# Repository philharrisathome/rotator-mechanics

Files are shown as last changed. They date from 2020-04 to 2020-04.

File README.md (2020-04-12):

# rotator-mechanics

This is my branch of https://gitlab.com/librespacefoundation/satnogs/satnogs-rotator/-/tree/v3.1-pre-release, heavily modified for different drive motor strategy.

Full credit goes to the team at SatNOGS - if I can get this build working I'll look at merging it in.

---

# SatNOGS Rotator

Hardware for SatNOGS Rotator. This repository includes all needed source files for 3D printed (and other) parts of SatNOGS Rotator.

## Documentation

More information can be found in our [wiki](https://wiki.satnogs.org/SatNOGS_Rotator_v3).

## Repository policy - Naming Convention

According to F3 - [Form, Fit and function](https://en.wikipedia.org/wiki/Form,_fit_and_function) and
[Part number, wiki page](https://en.wikipedia.org/wiki/Part_number) some rules build about the naming
convention and versioning:
* C, custom parts, placed in rotator_parts file
* H, hardware parts, placed in shared file
* A, assemblies, placed in assemblies file
* All used part numbers are placed in part-number-list spreadsheet.
* Start the number from 1000, e.g. C1000-1.
* Dash -1 (odd), are parts from same family for example M5 screws with same DIN and different lengths.
* Dash -2 (even), are parts from same family but all features are mirrored.
* Small changes in the part (fit - aspect), not affect the part number but affected the variant (-n).
* Big changes in the part or assembly (form and function aspect), affect the part number, make a new one
and replace or remove the old one.
* When a part is ready, in the commit message only this part and the message contains the revision of the part and a
release note about the changes. If needed update the drawing inside the freecad.
Then commit all sub-assemblies and the main assembly which affected by the part or parts.
* In order to add a new part take a new part number according to the part number list (spreadsheet).
* When a part or assembly isn't ready for release, in commit message add WIP, work in progress, write the
changes must be done, refers to the issue.
* When all parts and assemblies are ready and working properly, a release is done with tagging the last commit
and a file with all fabrication files like *.stl, *.step, *.pdf (for drawings), *.dxf (for 2D parts) are generated
which each file is naming with pn_revN.*
* Master branch is most times under active development, so expect things to break.
* Assembly is broken down to specific groups, sub-assemlies. The first priority of assembly levels is to help the designer in
design process and not in the real assembly. The second priority is to make assemblies that helps in assembly process.
We never work on very large assemblies, due to limitation in CAD program.
* Try to use a coordinate system that is fit in the main assembly.
* Drawing revision does not exist, only part or assembly revision is modified. When a small change is done in drawing for example in text the revision isn't change because the part or assembly isn't change.

## Contribute

The main repository lives on [Gitlab](https://gitlab.com/librespacefoundation/satnogs/satnogs-rotator) and all Merge Request should happen there.

## License


Licensed under the [CERN OHLv1.2](LICENSE).

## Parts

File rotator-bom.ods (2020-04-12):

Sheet: DC Motor
Part | Qty To Buy | Qty In project | Sold in Packs of | Unit of Measure | Distributor | Ref | Distributor Ref | Project Section | Price | Cost to Project | Link
Aluminum Tube 6063 OD40 TH1.5 | 2 | 2 | 1 | PCE | Motedis | C1001-1 and C1001-3 | 2287 | Hardware | 0.9 | 1.8 | https://www.motedis.com/shop/Semi-finished-products/Circular-tube-anodized-DIN-6060/Circular-tube-40x15-anodized::1066.html
Shaft Side | 4 | 4 | 1 | PCE |  | C1010-3 |  | Custom Part |  | 0
Shaft Side Bearing Flange | 4 | 4 | 1 | PCE |  | C1011-3 |  | Custom Part |  | 0
Worm Wheel, 30T | 2 | 2 | 1 | PCE |  | C1020-1 |  | Custom Part |  | 0
Shaft Collar ID40 | 2 | 2 | 1 | PCE |  | C1021-1 |  | Custom Part |  | 0
Shaft Washer ID40 OD50 | 2 | 2 | 1 | PCE |  | C1022-1 |  | Custom Part |  | 0
Motor Mount | 2 | 2 | 1 | PCE |  | C1030-1 |  | Custom Part |  | 0
Encoder Gear | 2 | 2 | 1 | PCE |  | C1040-1 |  | Custom Part |  | 0
Homing Pin | 2 | 2 | 1 | PCE |  | C1041-1 |  | Custom Part |  | 0
End-Stop Mount | 2 | 2 | 1 | PCE |  | C1042-1 |  | Custom Part |  | 0
Encoder Mount | 2 | 2 | 1 | PCE |  | C1043-1 |  | Custom Part |  | 0
Aluminum Profil 20x20 B-type slot 6 L100 | 18 | 18 | 1 | PCE | Motedis | C1050-1 | 22206 | Custom Part | 0.3 | 5.4 | https://www.motedis.com/shop/Slot-profiles/Profile-20-B-Type-slot-6/Profile-20x20-B-type-slot-6::1.html
Aluminum Profil 20x20 B-type slot 6 L140 | 8 | 8 | 1 | PCE | Motedis | C1050-5 | 22206 | Custom Part | 0.45 | 3.6 | https://www.motedis.com/shop/Slot-profiles/Profile-20-B-Type-slot-6/Profile-20x20-B-type-slot-6::1.html
Threaded rod M5 DIN975 INOX A2, Worm Gear Shaft | 1 | 1 | 1 | m |  | C1060-1 |  | Hardware | 2.5 | 2.5
Worm Mount | 4 | 4 | 1 | PCE |  | C1061-3 and C1061-4 |  | Custom Part |  | 0
Worm Gear | 2 | 2 | 1 | PCE |  | C1062-1 |  | Custom Part | 10 | 20 | https://www.shapeways.com/
Deep groove ball bearing 625zz | 4 | 4 | 1 | PCE |  | H1011-1 |  | Hardware | 0.6 | 2.4
Deep groove ball bearing 6008zz | 4 | 4 | 1 | PCE |  | H1012-1 |  | Hardware | 4 | 16
Inner bracket B-type Tslot6 | 40 | 40 | 1 | PCE | Motedis | H1020-1 | 099I9006 | Hardware | 0.5 | 20 | https://www.motedis.com/shop/Slot-profile-accessories/Accessories-20-B-Typ-slot-6/Inner-bracket-20-steel-B-Type-slot-6::562.html
T-nut B-type slot 6 M4 | 32 | 32 | 1 | PCE | Motedis | H1021-1 | 096H06410 | Hardware | 0.2 | 6.4 | https://www.motedis.com/shop/Slot-profile-accessories/Accessories-20-B-Typ-slot-6/T-nut-B-type-slot-6-M4::555.html
M5 Nut DIN934 | 4 | 4 | 1 | PCE |  | H1030-1 |  | Hardware | 0.03 | 0.12
M5 Washer DIN125 | 6 | 6 | 1 | PCE |  | H1031-1 |  | Hardware | 0.03 | 0.18
Timing Pulley GT2 36T, bore 5mm, belt wide 6mm | 2 | 2 | 1 | PCE |  | H1040-1 |  | Hardware | 4.2 | 8.4
Timing Belt GT2, Wide 6mm, Length 158mm, Teeth 79 | 2 | 2 | 1 | PCE |  | H1200-1 |  | Hardware | 1.5 | 3
M3 Nut DIN934 | 26 | 26 | 1 | PCE |  | H1070-1 |  | Hardware | 0.03 | 0.78
M4 Nut DIN934 | 24 | 24 | 1 | PCE |  | H1080-1 |  | Hardware | 0.03 | 0.72
Set Screw M3 L10 DIN 914 | 16 | 16 | 1 | PCE |  | H1090-1 |  | Hardware | 0.2 | 3.2
Screw M4 L25 DIN912 | 16 | 16 | 1 | PCE |  | H1100-1 |  | Hardware | 0.05 | 0.8
Screw M4 L20 DIN912 | 8 | 8 | 1 | PCE |  | H1100-3 |  | Hardware | 0.07 | 0.56
Screw M4 L10 DIN912 | 30 | 30 | 1 | PCE |  | H1100-5 |  | Hardware | 0.08 | 2.4
Washer M4 DIN125 | 34 | 34 | 1 | PCE |  | H1110-1 |  | Hardware | 0.03 | 1.02
Screw M3 L10 DIN912 | 8 | 8 | 1 | PCE |  | H1120-1 |  | Hardware | 0.04 | 0.32
Screw M3 L12 DIN912 | 4 | 4 | 1 | PCE |  | H1120-3 |  | Hardware | 0.04 | 0.16
Washer M3 DIN125 | 12 | 12 | 1 | PCE |  | H1130-1 |  | Hardware | 0.03 | 0.36
U Bolts Clamp for 40mm Tube | 4 | 4 | 1 | PCE |  | H1060-1 |  | Hardware | 2 | 8
CAT5e UTP cable | 6 | 6 | 1 | m |  | H1170-5 |  | Electronics | 0.16 | 0.96
End stop switch SS0505 | 2 | 2 | 1 | PCE | HIGHLY | H1050-1 | SS0505A | Electronics | 0.7 | 1.4
Heat-shrinkable, OD 6.4mm for CAT5E cable | 1 | 1 | 1 | m |  | H1160-3 |  | Electronics | 0.3 | 0.3
Heat-shrinkable, OD 4.8mm, for end-stop cables | 1 | 1 | 1 | m |  | H1160-5 |  | Electronics | 0.25 | 0.25
Crimps for Dupont Female 2.54 pitch | 38 | 38 | 1 | PCE | pololu | H1180-1 | 1930 | Electronics | 0.06 | 2.28 | https://www.pololu.com/product/1930
Dupont, Housing Wire Female 4 Pins 2.54mm (2x2P) | 5 | 5 | 1 | PCE | pololu | H1190-1 | 1910 | Electronics | 0.06 | 0.3
Dupont, Housing Wire Female 3 Pins 2.54mm (1x3P) | 6 | 6 | 1 | PCE | pololu | H1190-3 | 1902 | Electronics | 0.04 | 0.24
ABS Filament for FDM 3D-printer | 1 | 1 | 1 | Kg |  | - |  | Hardware | 17 | 17
DC motor adapter | 2 | 2 | 1 | PCE |  | C1070-1 |  | Custom Part |  | 0
DC motor cover part #1 | 2 | 2 | 1 | PCE |  | C1071-1 |  | Custom Part |  | 0
DC motor cover part #2 | 2 | 2 | 1 | PCE |  | C1072-1 |  | Custom Part |  | 0
DC motor, D37mm L54mm, Gear ratio 50:1, 12V 200RPM 1.2Nm | 2 | 2 | 1 | PCE | pololu | H1001-1 | 1104 | Electronics | 25 | 50 | https://www.pololu.com/product/1104
Timing Pulley GT2 20T, bore 6mm, Belt width 6mm | 2 | 2 | 1 | PCE |  | H1041-3 |  | Hardware | 2.6 | 5.2
Screw M3L6 DIN965 | 8 | 8 | 1 | PCE |  | H1140-1 |  | Hardware | 0.04 | 0.32
Capacitor, MLCC - Leaded 0.1uF 50volts X7R 10% 5.0mm L/S | 2 | 2 | 1 | PCE | Mouser | H1150-1 | 75-1C20X7R104K050B | Electronics | 0.15 | 0.3 | https://gr.mouser.com/ProductDetail/Vishay-Sprague/1C20X7R104K050B/
Heat-shrinkable, OD 38.1mm | 1 | 1 | 1 | m |  | H1160-1 |  | Electronics | 1.8 | 1.8
Stranded Cable ~1.5mm^2 (16AWG) – Red | 1 | 1 | 1 | m |  | H1170-1 |  | Electronics | 0.5 | 0.5
Stranded Cable ~1.5mm^2 (16AWG) – Black | 1 | 1 | 1 | m |  | H1170-1 |  | Electronics | 0.5 | 0.5
 |  |  |  |  |  |  |  |  | Total | 188.97

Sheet: Stepper Motor
Part | Qty To Buy | Qty In project | Sold in Packs of | Unit of Measure | Distributor | Ref | Distributor Ref | Project Section | Price | Cost to Project | Link
Aluminum Tube 6063 OD40 TH1.5 | 2 | 2 | 1 | PCE | Motedis | C1001-1 and C1001-3 | 2287 | Hardware | 0.9 | 1.8 | https://www.motedis.com/shop/Semi-finished-products/Circular-tube-anodized-DIN-6060/Circular-tube-40x15-anodized::1066.html
Shaft Side | 4 | 4 | 1 | PCE |  | C1010-3 |  | Custom Part |  | 0
Shaft Side Bearing Flange | 4 | 4 | 1 | PCE |  | C1011-3 |  | Custom Part |  | 0
Worm Wheel, 30T | 2 | 2 | 1 | PCE |  | C1020-1 |  | Custom Part |  | 0
Shaft Collar ID40 | 2 | 2 | 1 | PCE |  | C1021-1 |  | Custom Part |  | 0
Shaft Washer ID40 OD50 | 2 | 2 | 1 | PCE |  | C1022-1 |  | Custom Part |  | 0
Motor Mount | 2 | 2 | 1 | PCE |  | C1030-1 |  | Custom Part |  | 0
Encoder Gear | 2 | 2 | 1 | PCE |  | C1040-1 |  | Custom Part |  | 0
Homing Pin | 2 | 2 | 1 | PCE |  | C1041-1 |  | Custom Part |  | 0
End-Stop Mount | 2 | 2 | 1 | PCE |  | C1042-1 |  | Custom Part |  | 0
Encoder Mount | 2 | 2 | 1 | PCE |  | C1043-1 |  | Custom Part |  | 0
Aluminum Profil 20x20 B-type slot 6 L100 | 18 | 18 | 1 | PCE | Motedis | C1050-1 | 22206 | Custom Part | 0.3 | 5.4 | https://www.motedis.com/shop/Slot-profiles/Profile-20-B-Type-slot-6/Profile-20x20-B-type-slot-6::1.html
Aluminum Profil 20x20 B-type slot 6 L140 | 8 | 8 | 1 | PCE | Motedis | C1050-5 | 22206 | Custom Part | 0.45 | 3.6 | https://www.motedis.com/shop/Slot-profiles/Profile-20-B-Type-slot-6/Profile-20x20-B-type-slot-6::1.html
Threaded rod M5 DIN975 INOX A2, Worm Gear Shaft | 1 | 1 | 1 | m |  | C1060-1 |  | Hardware | 2.5 | 2.5
Worm Mount | 4 | 4 | 1 | PCE |  | C1061-3 and C1061-4 |  | Custom Part |  | 0
Worm Gear | 2 | 2 | 1 | PCE |  | C1062-1 |  | Custom Part | 10 | 20 | https://www.shapeways.com/
Deep groove ball bearing 625zz | 4 | 4 | 1 | PCE |  | H1011-1 |  | Hardware | 0.6 | 2.4
Deep groove ball bearing 6008zz | 4 | 4 | 1 | PCE |  | H1012-1 |  | Hardware | 4 | 16
Inner bracket B-type Tslot6 | 40 | 40 | 1 | PCE | Motedis | H1020-1 | 099I9006 | Hardware | 0.5 | 20 | https://www.motedis.com/shop/Slot-profile-accessories/Accessories-20-B-Typ-slot-6/Inner-bracket-20-steel-B-Type-slot-6::562.html
T-nut B-type slot 6 M4 | 32 | 32 | 1 | PCE | Motedis | H1021-1 | 096H06410 | Hardware | 0.2 | 6.4 | https://www.motedis.com/shop/Slot-profile-accessories/Accessories-20-B-Typ-slot-6/T-nut-B-type-slot-6-M4::555.html
M5 Nut DIN934 | 4 | 4 | 1 | PCE |  | H1030-1 |  | Hardware | 0.03 | 0.12
M5 Washer DIN125 | 6 | 6 | 1 | PCE |  | H1031-1 |  | Hardware | 0.03 | 0.18
Timing Pulley GT2 36T, bore 5mm, belt wide 6mm | 2 | 2 | 1 | PCE |  | H1040-1 |  | Hardware | 4.2 | 8.4
Timing Belt GT2, Wide 6mm, Length 158mm, Teeth 79 | 2 | 2 | 1 | PCE |  | H1200-1 |  | Hardware | 1.5 | 3
M3 Nut DIN934 | 26 | 26 | 1 | PCE |  | H1070-1 |  | Hardware | 0.03 | 0.78
M4 Nut DIN934 | 24 | 24 | 1 | PCE |  | H1080-1 |  | Hardware | 0.03 | 0.72
Set Screw M3 L10 DIN 914 | 16 | 16 | 1 | PCE |  | H1090-1 |  | Hardware | 0.2 | 3.2
Screw M4 L25 DIN912 | 16 | 16 | 1 | PCE |  | H1100-1 |  | Hardware | 0.05 | 0.8
Screw M4 L20 DIN912 | 8 | 8 | 1 | PCE |  | H1100-3 |  | Hardware | 0.07 | 0.56
Screw M4 L10 DIN912 | 30 | 30 | 1 | PCE |  | H1100-5 |  | Hardware | 0.08 | 2.4
Washer M4 DIN125 | 34 | 34 | 1 | PCE |  | H1110-1 |  | Hardware | 0.03 | 1.02
Screw M3 L10 DIN912 | 8 | 8 | 1 | PCE |  | H1120-1 |  | Hardware | 0.04 | 0.32
Screw M3 L12 DIN912 | 4 | 4 | 1 | PCE |  | H1120-3 |  | Hardware | 0.04 | 0.16
Washer M3 DIN125 | 12 | 12 | 1 | PCE |  | H1130-1 |  | Hardware | 0.03 | 0.36
U Bolts Clamp for 40mm Tube | 4 | 4 | 1 | PCE |  | H1060-1 |  | Hardware | 2 | 8
CAT5e UTP cable | 6 | 6 | 1 | m |  | H1170-5 |  | Electronics | 0.16 | 0.96
End stop switch SS0505 | 2 | 2 | 1 | PCE | HIGHLY | H1050-1 | SS0505A | Electronics | 0.7 | 1.4
Heat-shrinkable, OD 6.4mm for CAT5E cable | 1 | 1 | 1 | m |  | H1160-3 |  | Electronics | 0.3 | 0.3
Heat-shrinkable, OD 4.8mm, for end-stop cables | 1 | 1 | 1 | m |  | H1160-5 |  | Electronics | 0.25 | 0.25
Crimps for Dupont Female 2.54 pitch | 38 | 38 | 1 | PCE | pololu | H1180-1 | 1930 | Electronics | 0.06 | 2.28 | https://www.pololu.com/product/1930
Dupont, Housing Wire Female 4 Pins 2.54mm (2x2P) | 5 | 5 | 1 | PCE | pololu | H1190-1 | 1910 | Electronics | 0.06 | 0.3
Dupont, Housing Wire Female 3 Pins 2.54mm (1x3P) | 6 | 6 | 1 | PCE | pololu | H1190-3 | 1902 | Electronics | 0.04 | 0.24
ABS Filament for FDM 3D-printer | 1 | 1 | 1 | Kg |  | - |  | Hardware | 17 | 17
Stepper motor NEMA17, L47mm, 1.8deg step angle, D-shaft 5mm, Max torque 0.48Nm, without cables | 2 | 2 | 1 | PCE | GRobotronics | H1003-1 | 14-00010849 | Hardware | 16 | 32 | https://grobotronics.com/stepper-motor-42byghw804.html
Timing Pulley GT2 20T, bore 5mm, Belt width 6mm | 2 | 2 | 1 | PCE |  | H1041-1 |  | Hardware | 2.6 | 5.2
Cables 4P for Stepper Motor 70cm JST PH 6P-DUPONT | 2 | 2 | 1 | PCE | GRobotronics | H1170-3 | 19-00010760 | Electronics | 1.2 | 2.4 | https://grobotronics.com/wire-4p-for-stepper-motor-70cm-jst-ph-6p-dupont.html
 |  |  |  |  |  |  |  |  | Total | 170.45

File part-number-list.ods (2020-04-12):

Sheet: Parts
Part Number | Description | Comments | QTY
C1001-1_symmetric_tube | Aluminium tube OD40mm TH1.5mm L240mm | Drawing | 1
C1001-3_asymmetric_tube | Aluminium tube OD40mm TH1.5mm L320mm | - | 1
C1010-1_shaft_side | Shaft deep groove ball bearing 6008zz mount | Layer height 0.4mm | 4
C1010-3 | Updated version of shaft side | Layer height 0.4mm | 4
C1011-1_shaft_bearing | Shaft deep groove ball bearing 6008zz mount | Layer height 0.4mm | 4
C1011-3 | Updated version of shaft side | Layer height 0.4mm | 4
C1020-1_shaft_gear | Worm wheel gear, 30T | Layer height 0.4mm | 2
C1021-1_shaft_collar | Worm wheel mount | Layer height 0.4mm, metric/imperial option | 2
C1022-1_shaft_spacer | Spacer or washer for shaft | Layer height 0.4mm, metric/imperial option | 2
C1022-3 | Updated version of shaft washer | Layer height 0.4mm or laser cuted | 2
C1030-1_motor_mount | Motor mount | Layer height 0.4mm | 2
C1040-1_encoder_gear | Encoder gear, slot to mount homing pin | Layer height 0.4mm, metric/imperial option | 2
C1041-1_homing_pin | Homing pin | Layer height 0.4mm, metric/imperial option | 2
C1042-1_endstop_mount | End stop mount | Layer height 0.4mm | 2
C1043-1_encoder_mount | Encoder mount | Layer height 0.4mm | 2
C1050-1_tslot6_100 | Aluprofil 20x20 B-Typ Nut 6 L100 | Drawing | 18
C1050-3_tslot6_160 | Aluprofil 20x20 B-Typ Nut 6 L160 | - | 8
C1050-5 | Updated version of C1050-3, L140 | - | 8
C1060-1_worm_shaft | Threaded rod M5 L100 for worm gear shaft | Drawing | 2
C1061-1_worm_mount | Worm mount | Layer height 0.4mm | 2
C1061-2_worm_mount | worm mount mirror part | Layer height 0.4mm | 2
C1061-3 | Updated version of C1061-1 | Layer height 0.4mm | 2
C1061-4 | Updated version of C1061-2 | Layer height 0.4mm | 2
C1062-1_worm_gear | Worm gear, is laser sintering part with nylon plastic | Laser sintering part, shapeways | 2
C1070-1_dc_motor_adapter | DC motor flange to mount in common stepper motor mount | Layer height 0.4mm | 2
C1071-1_dc_motor_cover | DC motor cover, part 1 | Layer height 0.4mm | 2
C1072-1_dc_motor_cover | DC motor cover, part 2 | Layer height 0.4mm | 2
C1080-1_cover_bottom | Cover box, bottom part | Sheet metal working, Drawing | 1
C1081-1_cover_top | Cover box, top part | Sheet metal working, Drawing | 1
C1082-1_cover_side | Cover box, side part | Sheet metal working, Drawing | 1
C1082-3_cover_side | Cover box, side part | Sheet metal working, Drawing | 1
C1082-5 | Cover box, side part, new revision of C1082-1 and -3 | Sheet metal working, Drawing | 2
C1083-1_shaft_seal | Shaft seal | Layer height 0.4mm, metric/imperial option | 3

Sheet: Hardware
Part Number | Description | Comments | QTY
H1001-1_dc_motor | DC motor, D37mm L54mm, Gear ratio 50:1 | DC motor D-Shaft | 2
H1003-1_stepper_motor_nema17 | Stepper motor NEMA17 | This stepper comes with D-Shaft and JST PH male connector on body of motor | 2
H1011-1_625zz | Deep groove ball bearing 625zz | Worm gear axis | 4
H1012-1_6008zz | Deep groove ball bearing 6008zz | Worm wheel axis | 4
H1020-1_Inner_bracket_btype_tslot6 | Inner bracket B-type Tslot6 |  | 44
H1021-1_bType_nut 6_M4 | B-Typ Nut 6/M4 |  | 32
H1030-1_nut_M5_din934 | Nut M5 DIN934 | Worm gear axis | 4
H1031-1_washer_M5_din125 | Washer M5 DIN125 | Worm gear axis | 6
H1040-1_pulley_gt2_36T | Timing Pulley GT2 36T, bore 5mm, belt width 6mm | Worm gear axis | 2
H1041-1_pulley_gt2_20T | Timing Pulley GT2 20T, bore 5mm, belt width 6mm | Stepper motor axis | 2
H1041-3_pulley_gt2_20T | Timing Pulley GT2 20T, bore 6mm, belt width 6mm | DC motor axis | 2
H1050-1_switch_SS0505 | End stop switch SS0505 |  | 2
H1060-1 | U Bolts Clamp | The model not exist in shared file | 4
H1070-1_nut_M3_din934 | Nut M3 DIN934 |  | 26
H1080-1_nut_M4_din934 | Nut M4 DIN934 |  | 24
H1090-1_set_screw_M3L10_din914 | Set Screw M3 L10 DIN914 |  | 16
H1100-1_screw_M4L25_din912 | Socket head screw M4 L25 DIN912 |  | 16
H1100-3_screw_M4L20_din912 | Socket head screw M4 L20 DIN912 |  | 8
H1100-5_screw_M4L10_din912 | Socket head screw M4 L10 DIN912 |  | 30
H1110-1_washer_M4_din125 | Washer M4 DIN125 |  | 34
H1120-1_screw_M3L10_din912 | Socket head screw M3 L10 DIN912 | For motor mount | 8
H1120-3_screw_M3L12_din912 | Socket head screw M3 L12 DIN912 | For end-stop | 4
H1130-1_washer_M3_din125 | Washer M3 DIN125 |  | 12
H1140-1_screw_M3L6_din965 | Phillips Flat Head Screw M3 L6 DIN965 | For DC motor flange | 8
H1150-1 | MLCC - Leaded 0.1uF 50volts X7R 10% 5.0mm L/S, for DC motors | mouser, model not exist in shared file (http://gr.mouser.com/ProductDetail/Vishay-Sprague/1C20X7R104K050B/) | 2
H1160-1 | Heat-shrinkable, OD 38.1mm, for DC motor wheather shielding | The part is assembled with C1071-1 and C1072-1 (per 1m), model not exist in shared file | 1
H1160-3 | Heat-shrinkable, OD 6.4mm for CAT5E cable | Per 1m, model not exist in shared file | 1
H1160-5 | Heat-shrinkable, OD 4.8mm, for cables, end stop | Per 1m, model not exist in shared file | 1
H1170-1 | Cables for DC motors, ~1.5mm^2 (16AWG) | Per 1m Black and per 1m Red, model not exist in shared file | 2
H1170-3 | Cables 4P for Stepper Motor 70cm (JST PH 6P-DUPONT) | The model not exist in shared file | 2
H1170-5 | CAT5e UTP cable for endstop, encoder, sensors and rotator cable | Per 1m, model not exist in shared file | 6
H1180-1 | Crimps for Dupont Female, 2.54mm pitch | The model not exist in shared file | 38
H1190-1 | Dupont, Housing Wire Female 4 Pins 2.54mm (2x2P) | The model not exist in shared file | 5
H1190-3 | Dupont, Housing Wire Female 3 Pins 2.54mm (1x3P) | The model not exist in shared file | 6
H1200-1 | Timing Belt GT2, Wide 6mm, Length 158mm, Teeth 79 | The model not exist in shared file | 1
H1210-1 | Phillips Rounded Head Screws for Sheet Metal, M3,5 X 6,5 | The model not exist in shared file | 12
H1220-1 | Slotted pin DIN1481, OD4 Χ L60, 0.14E PCE

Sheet: Assemblies
Part Number | Description | Comments | QTY
A1001-1_frame | Frame chassis sub assembly | Drawing | -
A1001-3_frame | Frame chassis sub assembly | Drawing | 2
A1010-1_worm_gear | Worm gear assembly | Drawing | 2
A1011-1_worm_mount | Worm mount assembly | Drawing | 2
A1011-2_worm_mount | Worm mount assembly, mirror | - | 2
A1020-1_shaft_collar | Shaft collar assembly for worm wheel | Drawing | 2
A1030-1_rotator_axis | Rotator axis assembly without frame, symmetric | Drawing | 2
A1030-3_rotator_axis | Rotator axis assembly without frame, asymmetric | - | 2
A1031-1_bearing_side | Bearing side assembly without end-stop and encoder mounts | Drawing | 2
A1032-1_bearing_side | Bearing side assembly with end-stop and encoder mounts | Drawing | 2
A1033-1_encoder_gear | Encoder gear assembly | Drawing | 2
A1040-1_symmetric_module | Rotator axis module with frame, symmetric | Drawing | 2
A1040-3_assymetric_module | Rotator axis module with frame, asymmetric | - | 2
A1050-1_az_el_rotator | Alt-Az antenna rotator | Drawing | 1
A1060-1_dc_motor | DC motor assembly | Drawing | 2
A1070-1_motor_mount | Motor Mount assembly | Drawing | 2

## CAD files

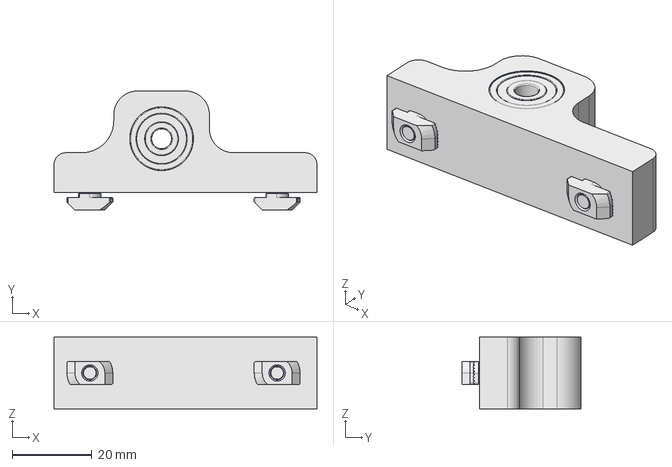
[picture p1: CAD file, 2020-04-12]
assemblies/A1011-1_worm_mount.fcstd
66.0 x 29.9 x 18.0 mm

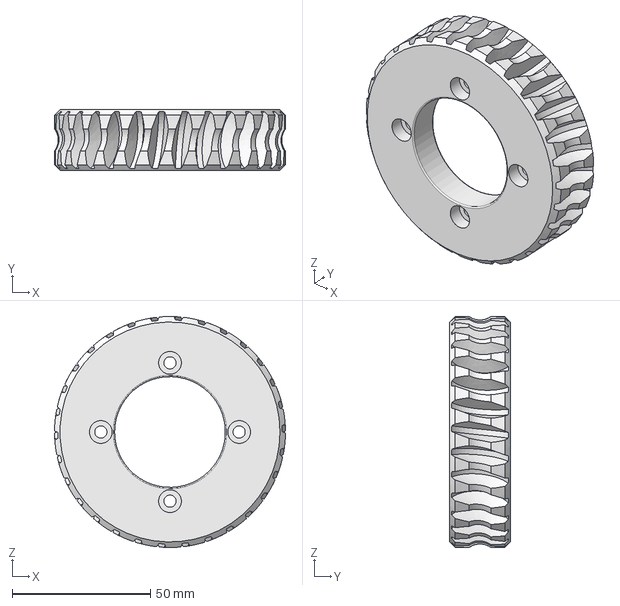
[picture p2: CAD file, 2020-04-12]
rotator_parts/C1020-1_shaft_gear.fcstd
83.5 x 22.0 x 83.5 mm

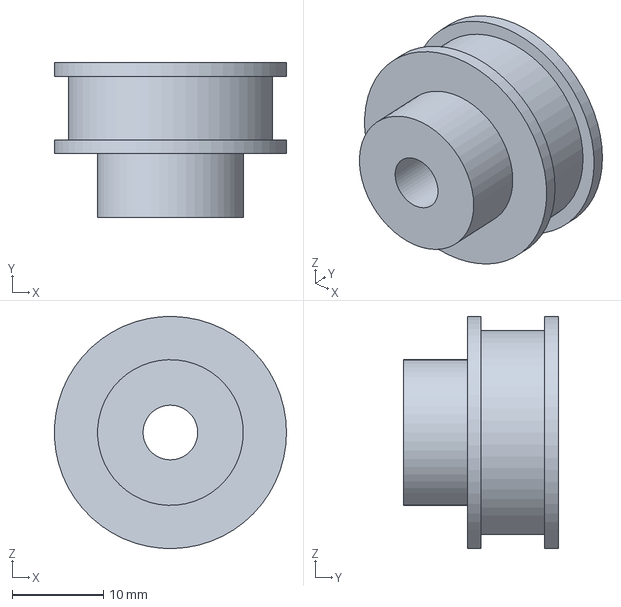
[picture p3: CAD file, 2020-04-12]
shared/H1040-1_pulley_gt2_36T.fcstd
25.5 x 17.0 x 25.5 mm

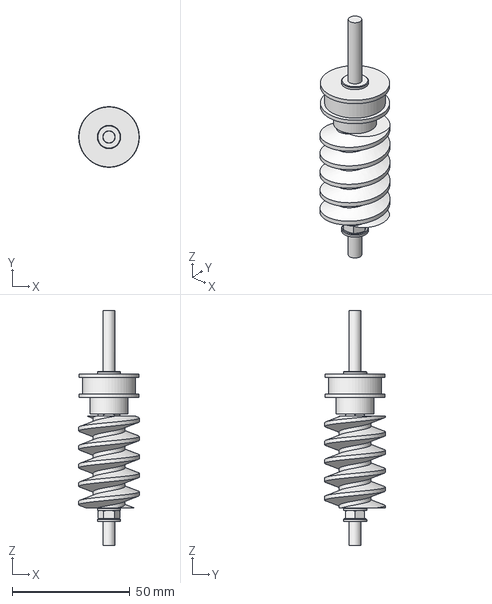
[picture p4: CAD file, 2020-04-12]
assemblies/A1010-1_worm_gear.fcstd
25.8 x 25.8 x 100.0 mm

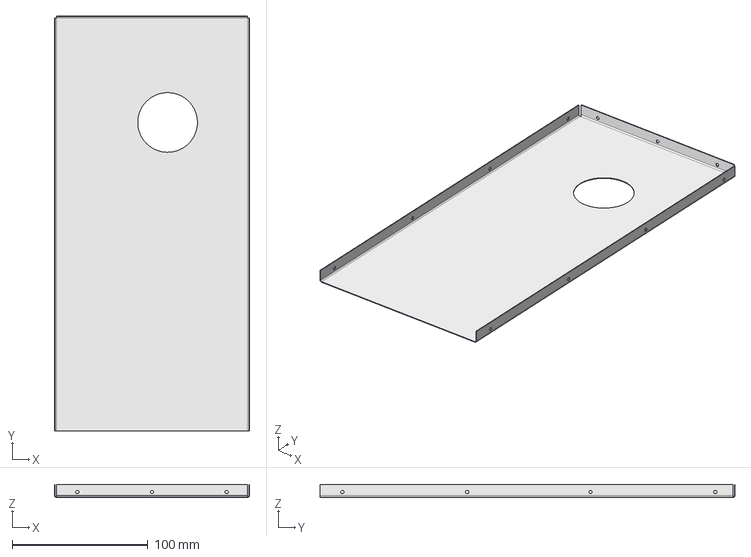
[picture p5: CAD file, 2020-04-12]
rotator_parts/C1082-1_cover_side.fcstd
144.0 x 306.0 x 9.50 mm

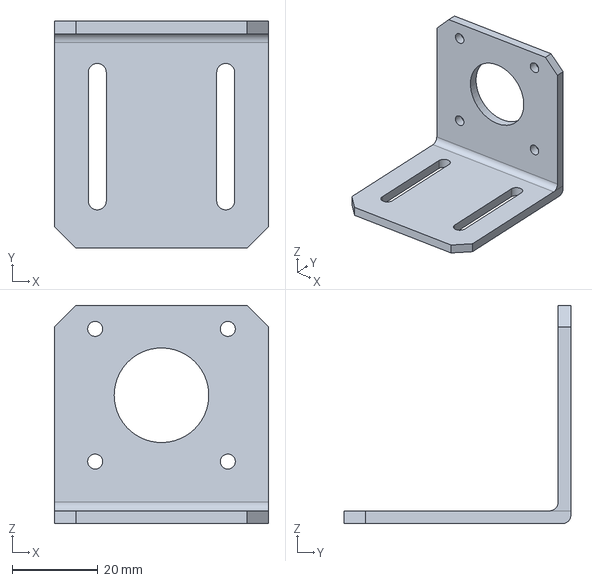
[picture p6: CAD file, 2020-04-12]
shared/H1002-1_motor_mount.fcstd
50.0 x 53.0 x 51.0 mm

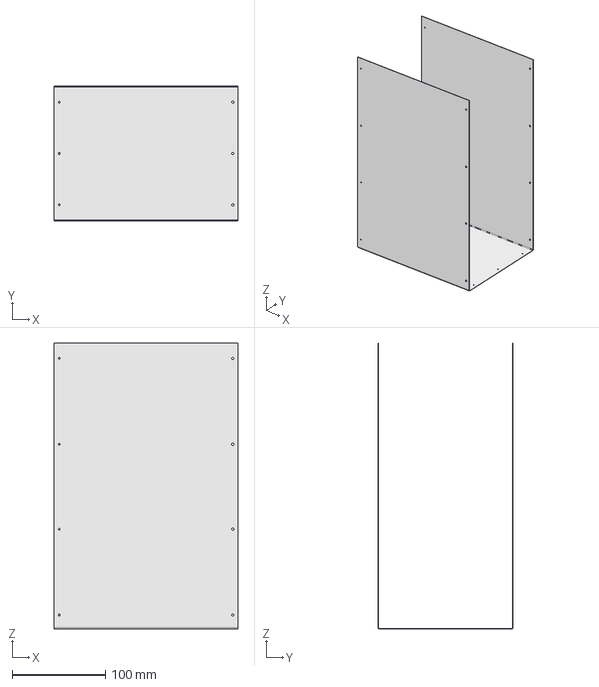
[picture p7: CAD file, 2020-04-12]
rotator_parts/C1081-1_cover_top.fcstd
197.0 x 145.0 x 306.5 mm

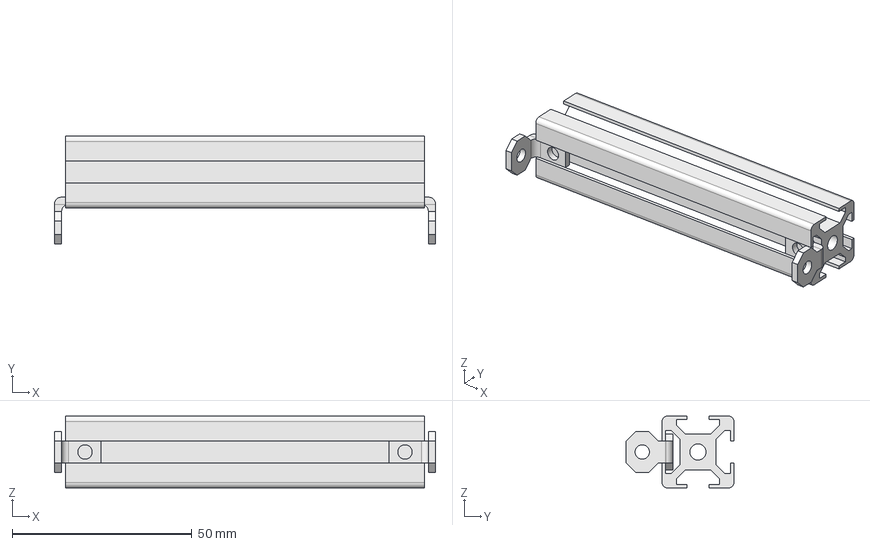
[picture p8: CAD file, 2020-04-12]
assemblies/A1001-1_frame.fcstd
106.0 x 30.0 x 20.0 mm

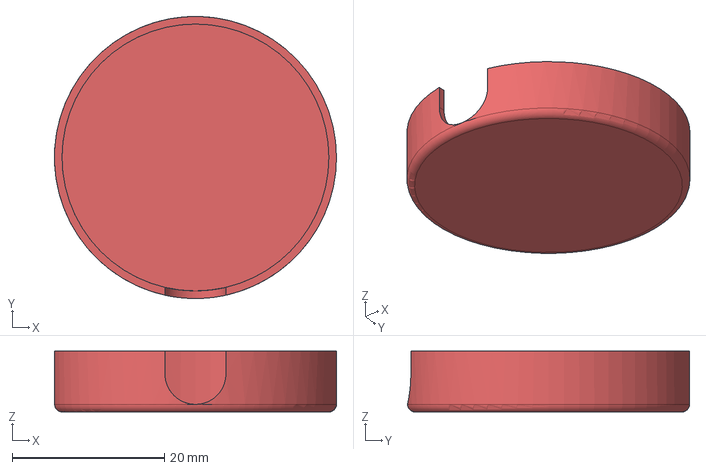
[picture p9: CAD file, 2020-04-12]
rotator_parts/C1072-1_dc_motor_cover.fcstd
37.0 x 37.0 x 8.00 mm

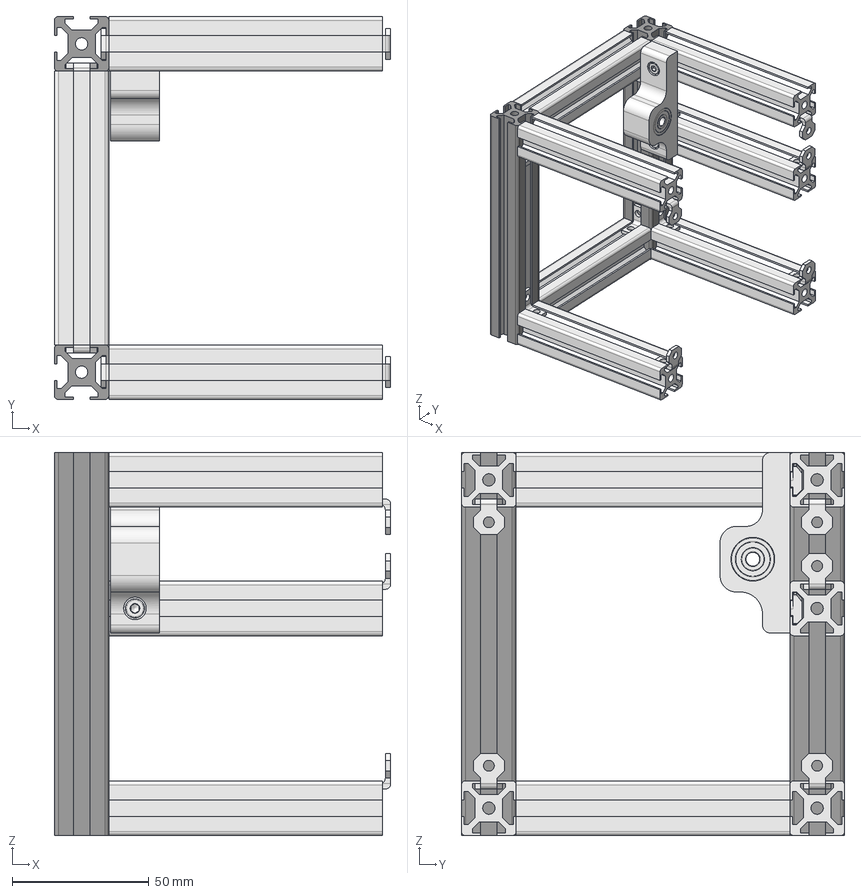
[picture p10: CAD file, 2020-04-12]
assemblies/A1001-3_frame.fcstd
123.0 x 140.0 x 140.0 mm
A1001-1
C1050-5
A1001_01
C1050_01
A1001_01001
A1001_02
A1001_03
A1001_04
A1011_1_worm_mount_01
A1001_1_frame_01

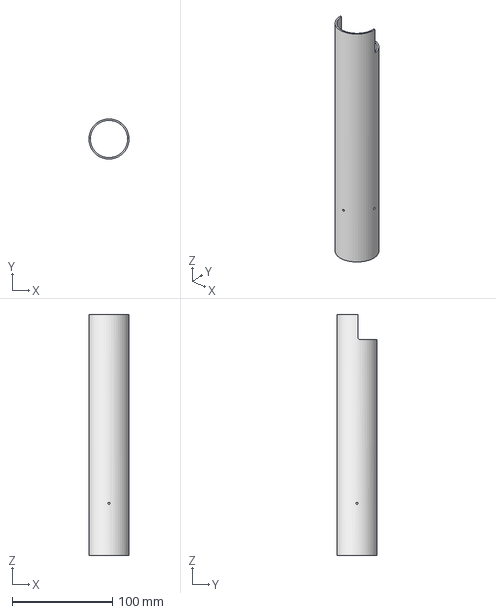
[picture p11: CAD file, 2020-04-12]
rotator_parts/C1001-3_asymmetric_tube.fcstd
40.0 x 40.0 x 240.0 mm

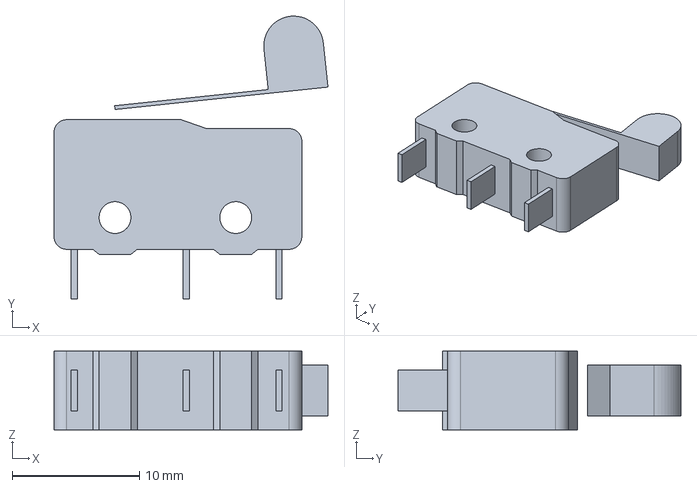
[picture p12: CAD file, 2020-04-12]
shared/H1050-1_switch_SS0505.fcstd
21.6 x 22.2 x 6.20 mm

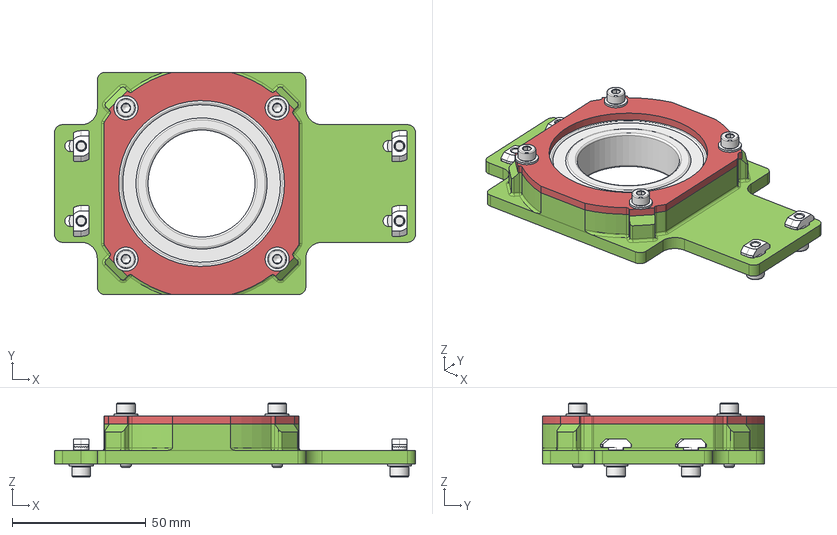
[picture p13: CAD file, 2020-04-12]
assemblies/A1031-1_bearing_side.fcstd
135.0 x 83.2 x 27.6 mm
C1010_3_01
H1080_1_nut_M4_din934_01
H1080_1_nut_M4_din934_02
H1080_1_nut_M4_din934_03
H1080_1_nut_M4_din934_04
H1011_1_6008zz_01
C1011_3_01
H1110_1_washer_M4_din125_01
H1110_1_washer_M4_din125_02
H1110_1_washer_M4_din125_03
H1110_1_washer_M4_din125_04
H1100_3_screw_M4L20_din912_01
H1100_3_screw_M4L20_din912_02
H1100_3_screw_M4L20_din912_03
H1100_3_screw_M4L20_din912_04
H1110_1_washer_M4_din125_05
H1110_1_washer_M4_din125_06
H1110_1_washer_M4_din125_07
H1110_1_washer_M4_din125_08
H1100_5_screw_M4L10_din912_01
H1100_5_screw_M4L10_din912_02
H1100_5_screw_M4L10_din912_03
H1100_5_screw_M4L10_din912_04
H1021_1_bType_nut_6_M4_01
H1021_1_bType_nut_6_M4_02
H1021_1_bType_nut_6_M4_03
H1021_1_bType_nut_6_M4_04

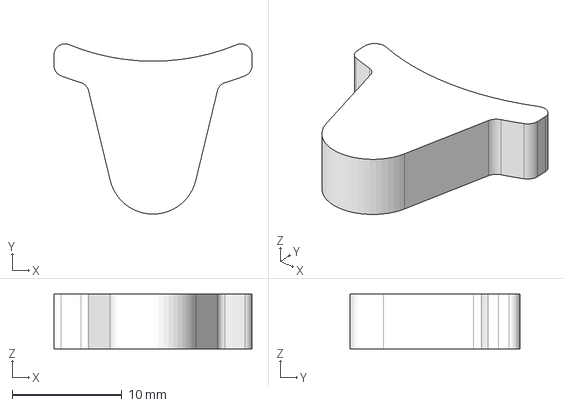
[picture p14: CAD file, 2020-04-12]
rotator_parts/C1041-1_homing_pin.fcstd
18.0 x 15.5 x 5.00 mm

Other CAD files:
assemblies/A1011-2_worm_mount.fcstd
shared/H1001-1_dc_motor.fcstd
assemblies/A1020-1_shaft_collar.fcstd
rotator_parts/C1043-1_encoder_mount.fcstd
assemblies/A1032-1_bearing_side.fcstd
assemblies/A1070-1_motor_mount.fcstd
rotator_parts/C1001-1_symmetric_tube.fcstd
rotator_parts/C1010-3.fcstd
rotator_parts/C1011-3.fcstd
rotator_parts/C1021-1_shaft_collar.fcstd
rotator_parts/C1022-3.fcstd
rotator_parts/C1030-1_motor_mount.fcstd
rotator_parts/C1042-1_endstop_mount.fcstd
rotator_parts/C1050-1_tslot6_100.fcstd
rotator_parts/C1050-5.fcstd
rotator_parts/C1060-1_worm_shaft.fcstd
rotator_parts/C1061-3.fcstd
rotator_parts/C1061-4.fcstd
rotator_parts/C1062-1_worm_gear.fcstd
rotator_parts/C1070-1_dc_motor_adapter.fcstd
rotator_parts/C1071-1_dc_motor_cover.fcstd
rotator_parts/C1080-1_cover_bottom.fcstd
rotator_parts/C1082-3_cover_side.fcstd
rotator_parts/C1083-1_shaft_seal.fcstd
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
